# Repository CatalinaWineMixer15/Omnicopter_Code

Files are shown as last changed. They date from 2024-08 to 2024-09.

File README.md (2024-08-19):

The zip file contains all of the python code necessary to get the omnicopter up and running with the MoCap system. It contains all of the different commands 
you could run in the MoCap room. In order to interface with the MoCap room at AFIT, you will need to go to http://www.nykl.net/aburn/ and follow Dr. Scott Nykl's instructions 
in his Youtube video (https://www.youtube.com/watch?v=hPGZf2dHSG0&t=637s). You might need Dr. Nykl's permission in order to access the aftrburner code. In the youtube video, 
you will only need to follow the instructions up until the 10:30 mark or so (before you compile the code). Once you follow the instructions, you will receive the 
optitrack_viewer program which allows you to connect to the cameras in the room. You will also need to have the Motive software running on a separate computer. In Motive, the 
omnicopter should be a defined object. If it is not, then you will need to build a new object for the omnicopter (see additional resources on how to do that). The 
omnicopter will have reflective markers around it, which allows the MoCap cameras to see the omnicopter.

Additionally, to access the flight control software running on the Kakute H7, you will need to connect your computer to the Kakute via USB and run QGroundControl. QGroundControl
can be downloaded from the following website: http://qgroundcontrol.com/

If you need to access the AM32 firmware on the ESCs, you can visit the following websites: https://esc-configurator.com/ or https://am32.ca/
You can use either website to access the firmware. **NOTE** AM32 can only be accessed when you have Betaflight running on your Kakute. It will not work with QGroundControl. You
must flash between the two FC softwares in order to access AM32. To flash Betaflight on the Kakute, you must first download the Betaflight configurator: https://betaflight.com/download
Once it is downloaded, hold down the bootloader button on the Kakute while connecting the USB cable from your computer. In the Betaflight configurator, you will see that the Kakute is
now in DFU mode. Go to the firmware flasher tab, choose the correct board and firmware version, and then click on 'Load Firmware [Online]'. Finally, flash the firmware and you should
have Betaflight on the Kakute once it is done flashing. In Betaflight, make sure to select an octocopter model. Otherwise, the AM32 firmware will not know how many motors you have on
the omnicopter. To flash back to QGroundControl/PX4, go back into the Betaflight configurator Firmware Flasher tab. Click on 'Load Firmware [Local]' and select the hex file that is
included in this repo titled 'holybro_kakuteh7_bootloader.hex'. You will then be able to connect to QGroundControl. In QGroundControl, go to the Firmware tab and select a custom
px4 file that is included in this repo titled 'holybro_kakuteh7_default.px4'. Lastly, go to the Parameters tab in QGroundControl and load the saved parameters. A copy of the latest
parameters titled 'kakuteh7Param.params' is included in this repo.

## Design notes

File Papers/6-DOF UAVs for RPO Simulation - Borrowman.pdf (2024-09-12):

### 6-DOF UAVs for RPO Simulation

### Matthew N. Borrowman Air Force Institute of Technology David H. Curtis Air Force Institute of Technology

ABSTRACT

Rendezvous and proximity operations (RPO) started early on in humans’ journey to space. This has allowed for satellites and spacecraft to dock with each other, and for us to build amazing machines. Among the things possible from this concept are the International Space Station and Hubble Telescope. The manning and upkeep of both rely on RPO to be completed consistently. Additionally, RPO is becoming increasingly useful in the military and private space sectors. However, hardware testing for close proximity trajectories can often be cost prohibitive. Using a 6 degree of freedom (DOF) unmanned aerial vehicle (UAV) to simulate spacecraft missions and test payloads helps alleviate testing costs and accelerate development. These UAVs, called omnicopters, can move in any direction at any arbitrary orientation. This allows for more accurate simulation of on-orbit conditions without being in space. These machines are relatively cheap to build and operate, costing no more than commercially available UAVs. This could not only help reduce the upfront research and development costs but also help increase the number of payloads that get to orbit. We have assembled the frame and components needed for the operation of the omnicopter but have not been able to get the software to operate as intended.

### 1. INTRODUCTION

John F. Kennedy’s famous “We Chose to go to the Moon” speech helped kick off a space race that eventually put humans on the moon. To achieve this feat, NASA had a lot to learn about space operations and what was truly possible. This resulted in a handful of years long programs and many manned space launches. They tested the physiological effects of space on humans, extravehicular activity, or space walks, and, in the late stages of the Gemini program, the ability of two spacecraft to meet up and dock while orbiting our planet.[6] The demonstration of RPO had implications that reached far beyond getting to the moon.

In the 1960’s, space travel was a wildly expensive endeavor. Everything had to be built from the ground up, and lessons about how to operate in space cost both money and lives. Today, space is frequented by both countries and companies, although this is primarily with unmanned operations. In recent years, the cost of a space launch has been reduced considerably through the advent of reusable booster rockets. However, getting to space is still expensive at about $1,500/kg to low earth orbit being the cheapest.[7] The cost of launch falls on top of the development of the spacecraft and their payloads themselves. Extensive testing is needed to ensure smooth operation of these payloads when they finally reach their destination in orbit. To accomplish this, both software and hardware simulations are carried out. Software simulation has relatively low barrier to entry and is quite cost effective as the computing power needed is easily accessible. However, hardware-in-the-loop testing remains an expensive and specialized undertaking. There are various forms of hardware testing that each have their own advantages and disadvantages. Air bearing platforms are commonly used but require a dedicated workspace and cannot actuate all six degrees of freedom.[8]

Ideally, the most accurate testing of hardware would be done in space itself. This would allow for the full 6-DOF behavior necessary to test a system in its entirety. However, in most cases this is not feasible due to the cost and dangers of failure. The various forms of RPO simulation help address the different kinds of tests needed to verify the performance of these spacecraft and their payloads.[2] Kinematic simulations deal with an external actuator implementing the translational and rotational characteristics of the spacecraft flight. Dynamic simulators rely on isolating the platform and use actuators that are representative of what the actual spacecraft uses.[5] These can also be combined into hybrid systems that allow for varied aspects of the spacecraft and payload to be tested. Other platforms are available, such as specialized aircraft operating in a parabolic flight path which helps simulate the microgravity/freefall environment. These aircraft are expensive to operate and only a few examples exist.

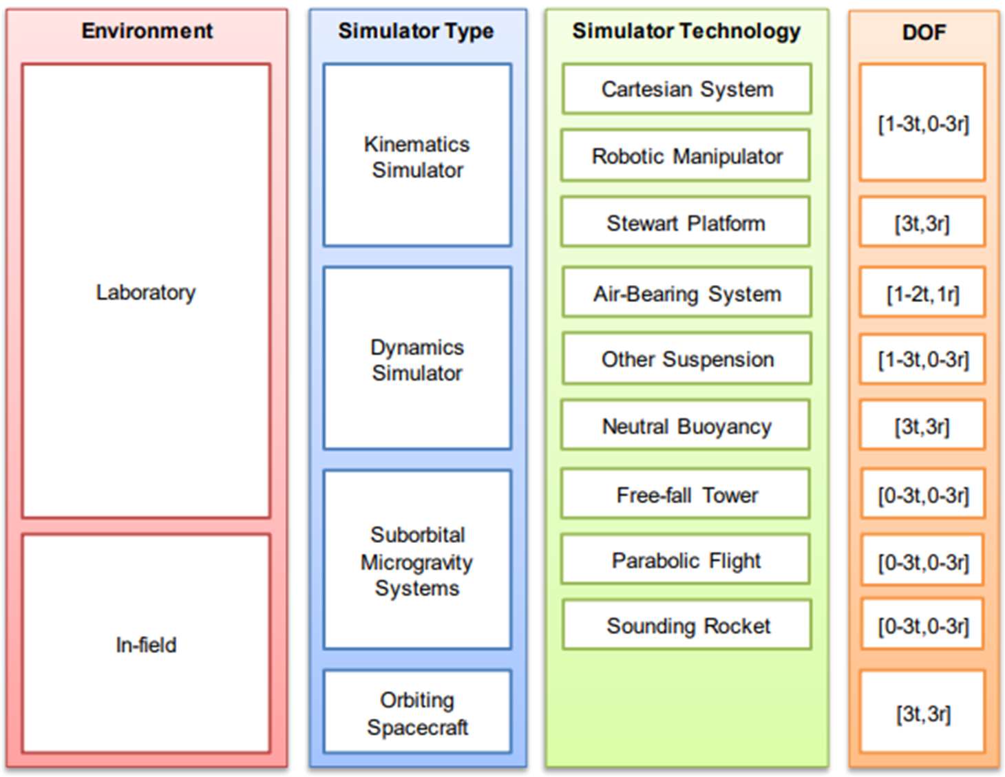
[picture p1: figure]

Figure 1. RPO Simulation Types[5]

The addition of a 6-DOF UAV, dubbed an omnicopter, could help with hardware testing. A drone that has command over the 6 degrees of freedom – 3 degrees of attitude and 3 degrees of position – is a relatively new concept with a handful of proven designs.[1][2] This opens a new avenue of hardware testing and simulation and helps address many problems that arise with the other testing methods. These drones are much more portable, cost-effective, and accessible than the dedicated testing facilities located at a handful of locations throughout the world. Additionally, multiple drones are able to be flown at the same time. This allows for multi-vehicle, 6-DOF, hardware simulations to be conducted. This has the potential to be a huge breakthrough for RPO simulation and component design. Before, almost all hardware simulations involved a singular moving vehicle.[5] Which is adequate for testing a singular payload, but testing multiple payloads designed to work in conjunction with each other is a more complicated endeavor.

### 2. METHODOLOGY

### 2.1 Design inspiration

While there are various 6-DOF UAV designs available, this project attempts to replicate the design of Brescianini and D'Andrea.[1] This design was chosen due to the availability of instruction on the build process as well as its demonstrated ability to operate with a payload. A few modifications were made for our specific design constraints, however due to the off-the-shelf nature of the build, there should not be any issue with using different parts. The open cube design and use of 8 props give it better lifting ability and modularity when compared to other designs that have been made. Examples of both can be seen in the figure below.

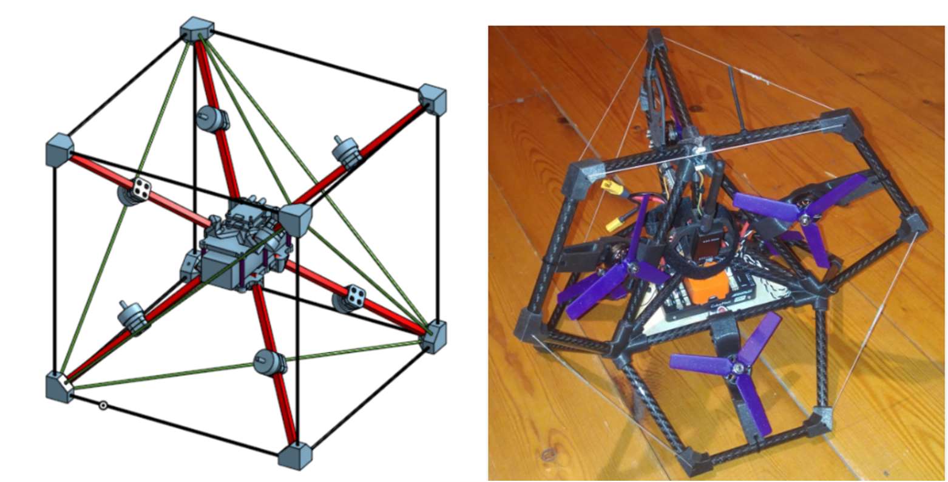
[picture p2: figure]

Figure 2. 6-DOF UAV designs[1]

The Brescianini and D'Andrea design can be seen on the left whereas the design on the right is from Peter Hall. Both utilize carbon fiber frames with 3D printed parts. However, the Brescianini and D'Andrea design is larger with the previously mentioned central area that could be payload capable. Hall’s design makes for a good 6-DOF demonstrator, but its utility outside of that scope is small. The control laws of the two designs are also significantly different due to the difference in the number of props.[1][4]

### 2.2 Starting the Build

Our build was guided by the PX4 write up that replicates the Brescianini and D’Andrea design. Included in this are complete 3D models of the system as well as STL files of all 3D printed parts. Below is the parts list.

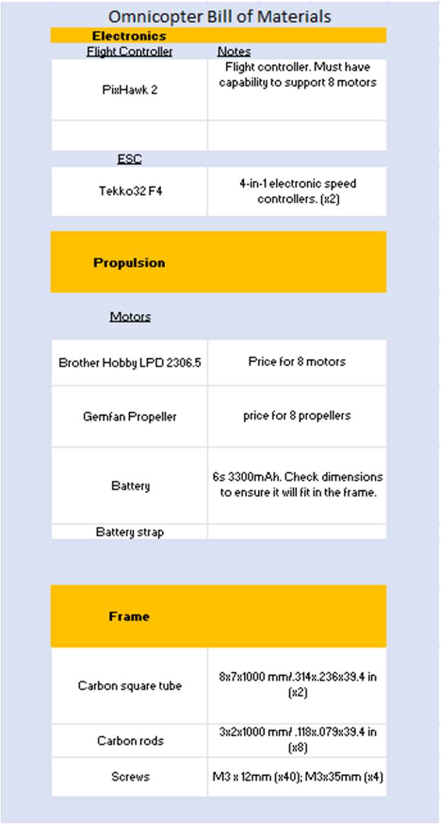
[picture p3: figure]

Figure 3. Omnicopter Parts List

The omnicopter utilizes 3D printed middle section plates, frame corners, and motor mounts. The middle section and the frame corners were printed with PLA and the motor mounts were printed with ABS. The carbon composite pieces that make up the frame were cut using a handheld rotary tool with a cutoff wheel. The eight, 8mm square tubes that the motors are mounted on are 240mm in length. The 3mm diameter rods that make up the exterior frame measure 328mm in length.

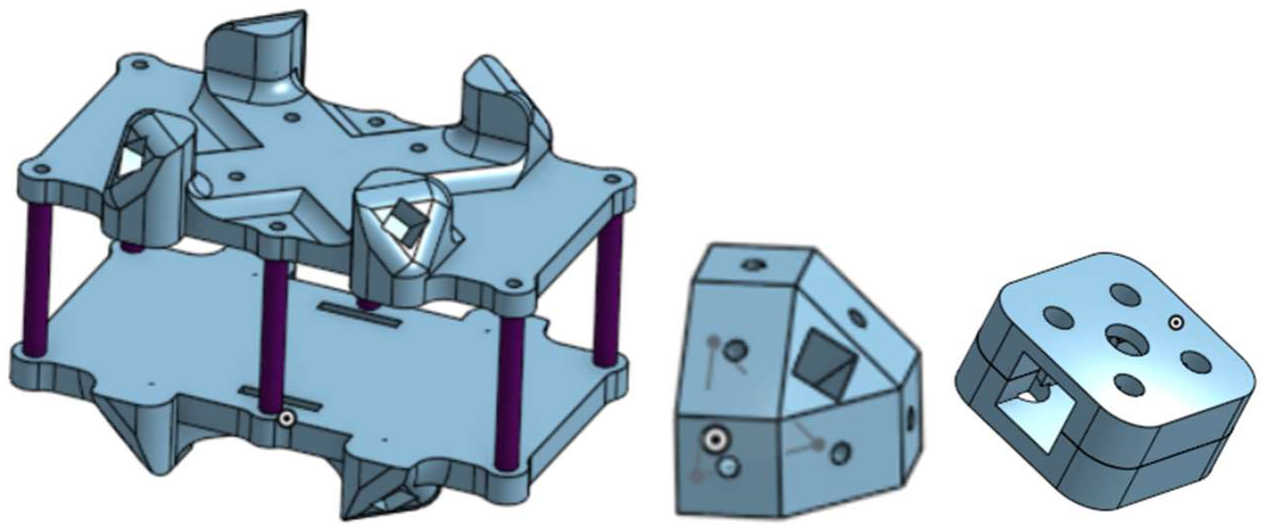
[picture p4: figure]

Figure 4. 3D Printed Assembly Parts

The motors were mounted using the 3D printed fitting shown on the right side of Figure 4. This simply clamps onto the square carbon tube with four screws. They were mounted as far away from the center as possible without the props breaking the plane of the exterior frame. It is important to mount the motors so their relative orientations are correct. Failure to do so would result in difficulty controlling the vehicle and potentially make it impossible to operate in 6 degrees of freedom.
The battery chosen was a 6s 3300mAh unit. This is mounted in the middle of the frame and held in place by the pressure from the top and bottom plates. Multiple manufacturers make this type of battery, but their dimensions can vary. It is important to verify that the battery will fit prior to purchase.
The electronic speed controllers (ESCs) were mounted on the top part of the middle section using 4 through bolts with the supplied vibration dampers. Two, 4-in-1 ESCs were used as a compact solution to power the 8 different motors. A battery connector was soldered onto the controllers, and a custom wiring harness was made to connect the ESCs to the motors.
A Pixhawk 2.1 auto pilot was used with a mini carrier board. This deviates from the original design and was used to satisfy the U.S. government purchasing requirements. The use of this part is suitable for the build, however there are lighter options available if purchasing requirements are not present. The Pixhawk was mounted on the bottom of the middle section using Velcro strips and further secured using a strip of tape. The default forward orientation of the Pixhawk was placed in such a way that the number 1 motor is in the most positive octant of the vehicle. A custom wiring harness was made to connect the ESCs to the auto pilot.

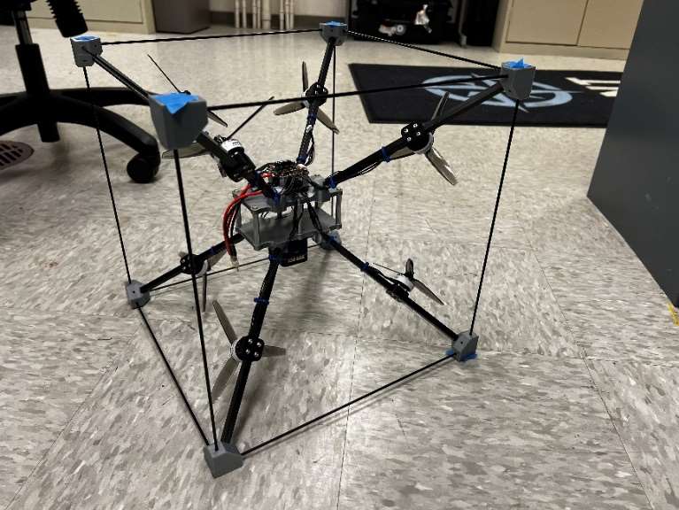
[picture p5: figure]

Figure 5. Omnicopter with ESCs and Autopilot Mounted

After mounting the auto pilot, a telemetry link was added. While there are many options for telemetry links, we tried to use the lightest solution we had on hand. The telemetry range and power requirements for this application are negligible. This telemetry link allows for the ground station to connect wirelessly to the auto pilot. This can be used to set up parameters for the operation of the omnicopter, as well as set up missions and flight paths.
These are the basic components needed for operation. Our design chose to use a Vicon chamber to give the autopilot positioning data in lieu of actual GPS connectivity. This decreases the weight of our design but also limits it to indoor operation. If outdoor operation is desired, a GPS antenna would be needed for the autopilot to get positioning data.
Programming the correct settings for the omnicopter is a difficult endeavor as there is not default omnicopter setting. Our build opted to use the QGroundControl ground station and run the PX4 firmware on the autopilot. For the airframe setup, a generic multi-rotor airframe much be chosen, and the motor positions need to be set up in a three-dimensional space instead of a coplanar setup found in most traditional multi-rotor aircraft.

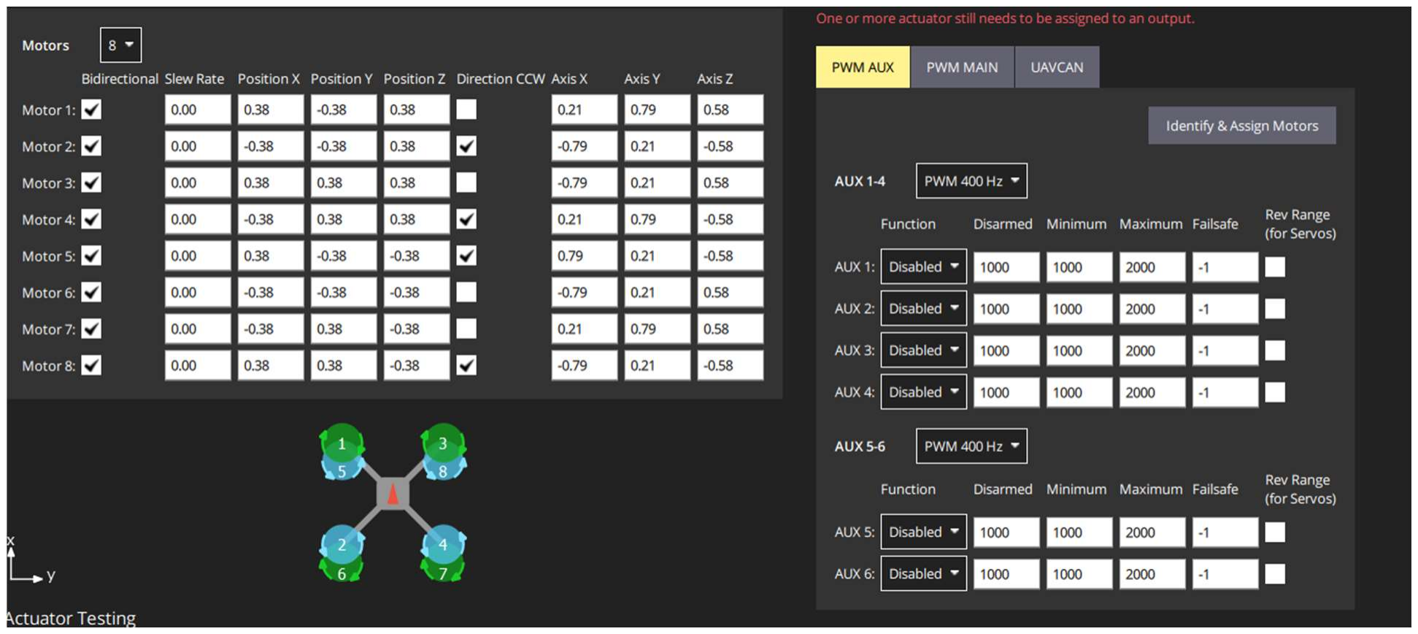
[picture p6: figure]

Figure 6. Omnicopter airframe setup

Using the indicated positive axis on the software, the known positive position of the autopilot, and the motor numbering scheme from the ESC data sheet, the location and orientations of the motors was able to be programmed. The positions are measured in feet from the center of the omnicopter. The orientation axes are normalized and based on where the motor shafts are pointing in relation to the positive axis of the omnicopter.

### 3. RESULTS

The omnicopter hardware has been assembled, however, it has not gotten off the ground yet. Our suspicion is that a failsafe is being triggered in the software that is preventing the system from operating. Our current troubleshooting hasn’t provided additional insight onto what the exact solution to this problem is.

### 4. CONCLUSIONS AND FUTURE WORK

The omnicopter is an ongoing design challenge. We hope to achieve the maiden flight soon and demonstrate the ability to manipulate the 6 degrees of freedom made possible with this design. After the flight characteristics have been figured out, we hope to add a payload. This could be an actuator or a sensor that could be used for testing. We also hope to make more examples and run multiple vehicle missions to simulate an on-orbit RPO.

### 5. REFERENCES

[1] Brescianini, D., and D’Andrea, R., Design, Modeling and Control of an Omni-Directional Aerial Vehicle. [2] | Christensen, Gargioni, Doyle, Schroeder and Black. "Space Simulation Overview: Leading Developments
| towards using Multi-Rotors to Simulate Space Vehicle Dynamics," AIAA 2020-1134. AIAA Scitech 2020 Forum. January 2020.
[3] Deans, C., Furgiuele, T., Doyle, D., and Black, J., Simulating omni-directional aerial vehicle operations for
| modeling satellite dynamics ASCEND 2020, 2020.
[4] E. Kaufman, K. Caldwell, D. Lee and T. Lee, Design and development of a free-floating hexrotor UAV for 6-
| DOF maneuvers, 2014 IEEE Aerospace Conference, Big Sky, MT, USA, 2014, pp. 1-10, doi: 10.1109/AERO.2014.6836427.
[5] Kwok Choon, Stephen & Wilde, Markus & Safbom, Conor & Romano, Marcello. (2020). Kinematic and
| Dynamic Spacecraft Maneuver Simulators for Verification and Validation of Space Robotic Systems. 10.2514/6.2020-1919.
[6] May. “What Was the Gemini Program” NASA Knows! August 2017
[7] Roberts, T., “Space Launch to Low Earth Orbit: How Much Does it Cost?” CSIS Aerospace Security Project,
| September 2022
[8] Rughani, R., Villafana, L., and Barnhart, D. A., “Swarm RPO and Docking Simulation on a 3DOF Air Bearing
| Platform,” International Astronautical Congress (IAC), 2019.

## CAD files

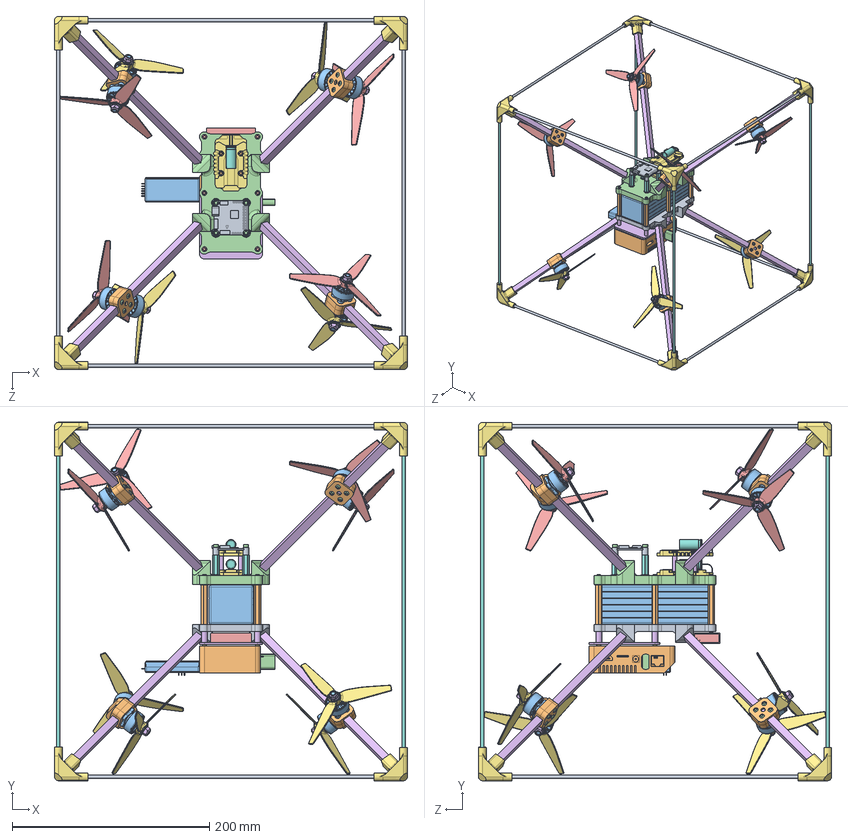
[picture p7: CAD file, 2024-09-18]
CAD/OmniFullWithMotors.SLDASM
358.1 x 363.7 x 358.2 mm
BottomBodyPlate_Simple
BodyPlate_Column x 6
BodyColumn_Washer x 10
ModifiedPart_Simple
BodyPlate_Bolt x 8
ODROID_Platform
BodyPlate_BottomBolt x 4
FC_Column x 4
FC_Board
ODROID
ODROID_SerialAdapter
ODROID_WifiModule
ODROID_SD_Card
ESC_Columns x 4
SkyStarsESC x 2
ESC_Capacitor x 2
ESC_BottomBolt x 4
ESC_TopBolt x 4
Battery
FC_Bolt2 x 8
JETI_Antenna
Rod x 8
CornerPart_v3_FlatCorner_2mmWall_3p5mmRod_p4mmTol x 8
Tube_Vert x 4
Tube_Horiz x 8
MotorMountPiece x 16
Motor x 8
Motor_Bolt x 32
PropCW x 4
MotorNut x 8
PropCCW x 4

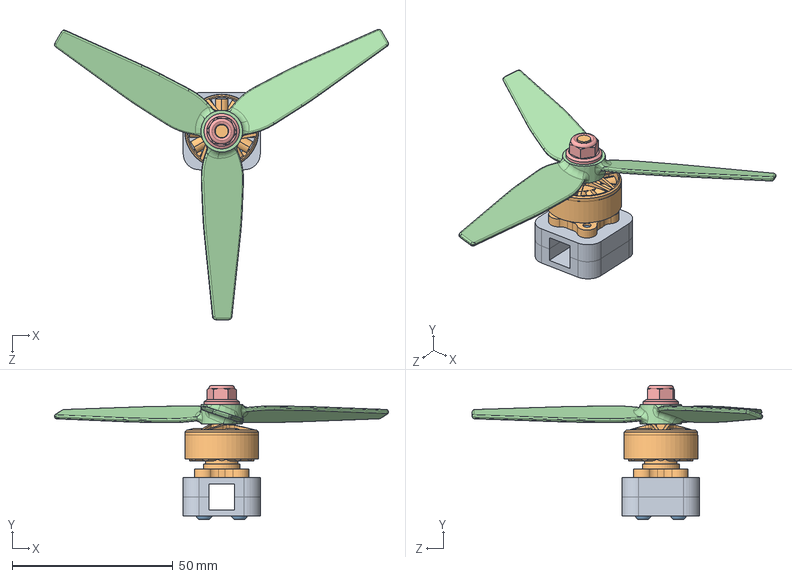
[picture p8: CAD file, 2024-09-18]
CAD/MotorAssemblyCW.SLDASM
103.9 x 41.9 x 90.4 mm
MotorMountPiece x 2
Motor
Motor_Bolt x 4
PropCW
MotorNut

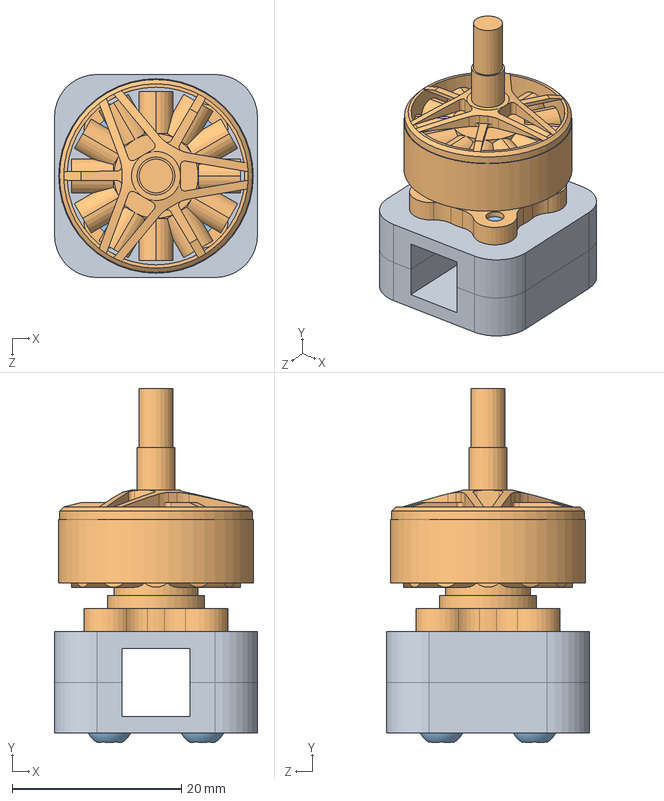
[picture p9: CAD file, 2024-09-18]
CAD/MotorAssembly.SLDASM
24.0 x 41.9 x 24.0 mm
MotorMountPiece x 2
Motor
Motor_Bolt x 4

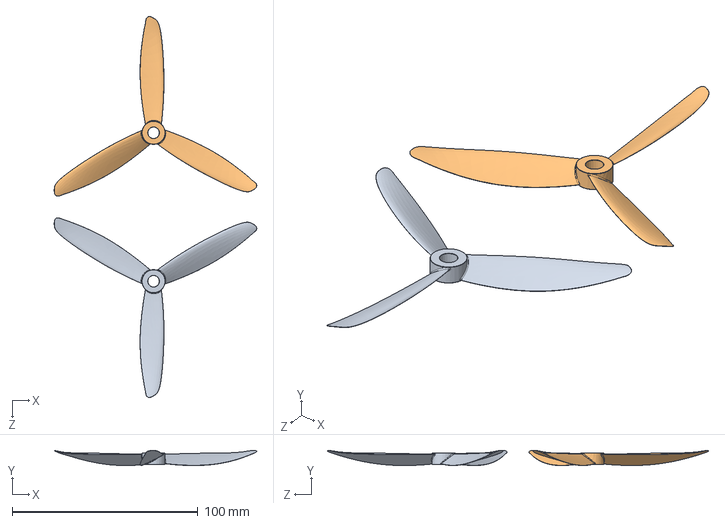
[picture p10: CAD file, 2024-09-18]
CAD/Tri-Blade 5045 Propeller CCW.SLDASM
109.2 x 8.15 x 205.3 mm
5045 CCW.step
5045 CW.step

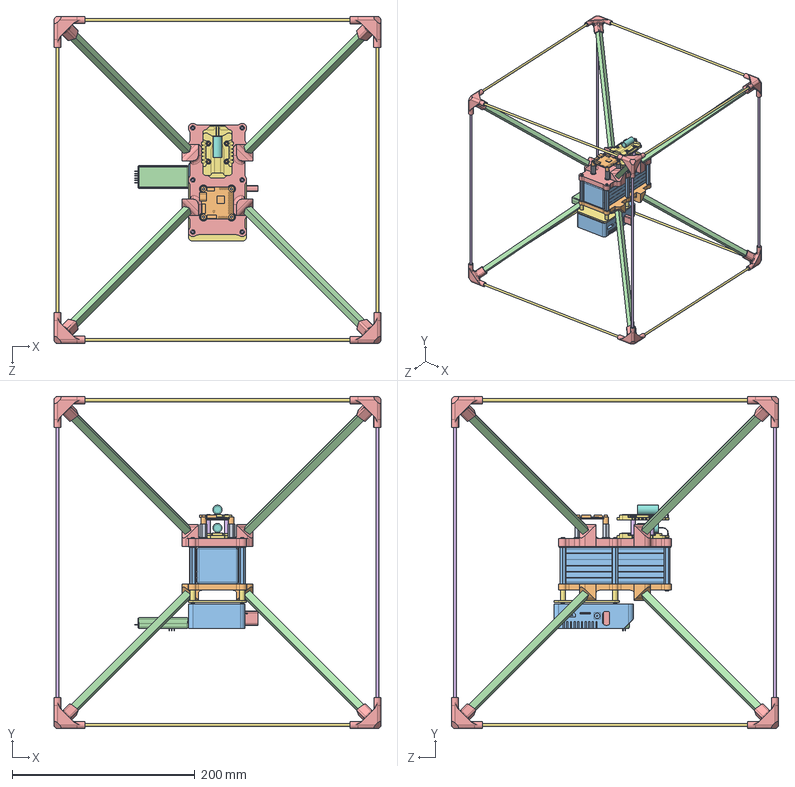
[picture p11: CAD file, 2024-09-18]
CAD/OmniFull.SLDASM
358.1 x 363.7 x 358.2 mm
BottomBodyPlate_Simple
BodyPlate_Column x 6
BodyColumn_Washer x 10
ModifiedPart_Simple
BodyPlate_Bolt x 8
ODROID_Platform
BodyPlate_BottomBolt x 4
FC_Column x 4
FC_Board
ODROID
ODROID_SerialAdapter
ODROID_WifiModule
ODROID_SD_Card
ESC_Columns x 4
SkyStarsESC x 2
ESC_Capacitor x 2
ESC_BottomBolt x 4
ESC_TopBolt x 4
Battery
Rod x 8
CornerPart_v3_FlatCorner_2mmWall_3p5mmRod_p4mmTol x 8
Tube_Vert x 4
Tube_Horiz x 8

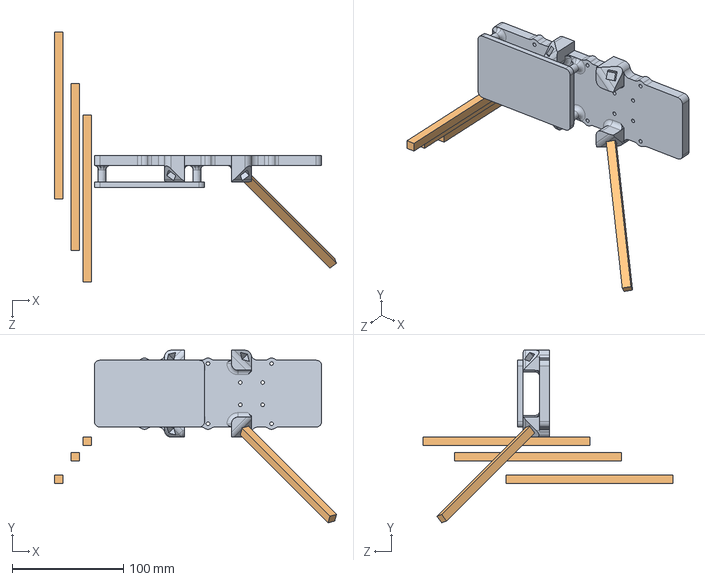
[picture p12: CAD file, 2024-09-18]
CAD/Omni.SLDASM
253.0 x 154.9 x 224.2 mm
ModifiedPart
Rod x 4

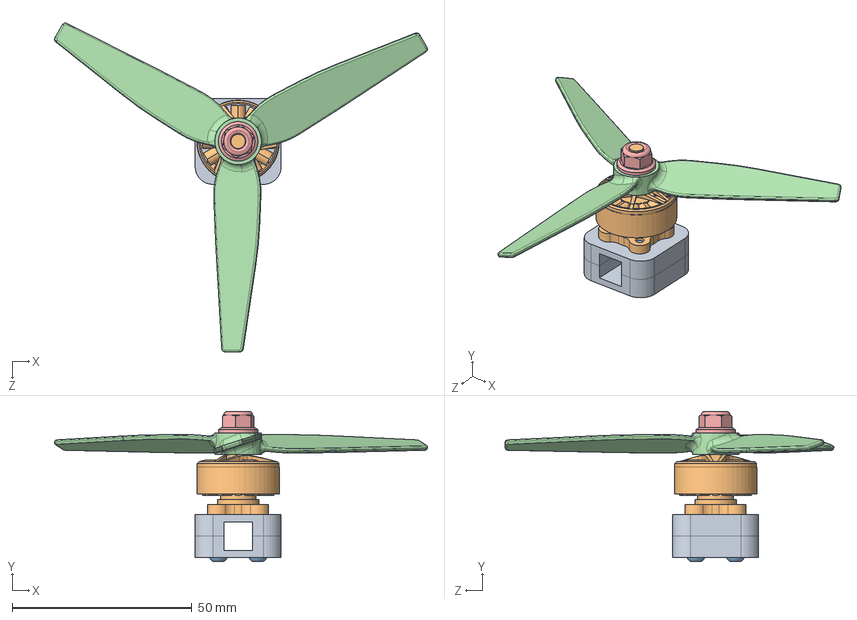
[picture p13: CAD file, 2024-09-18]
CAD/MotorAssemblyCCW.SLDASM
103.9 x 41.9 x 91.6 mm
MotorMountPiece x 2
Motor
Motor_Bolt x 4
PropCCW
MotorNut

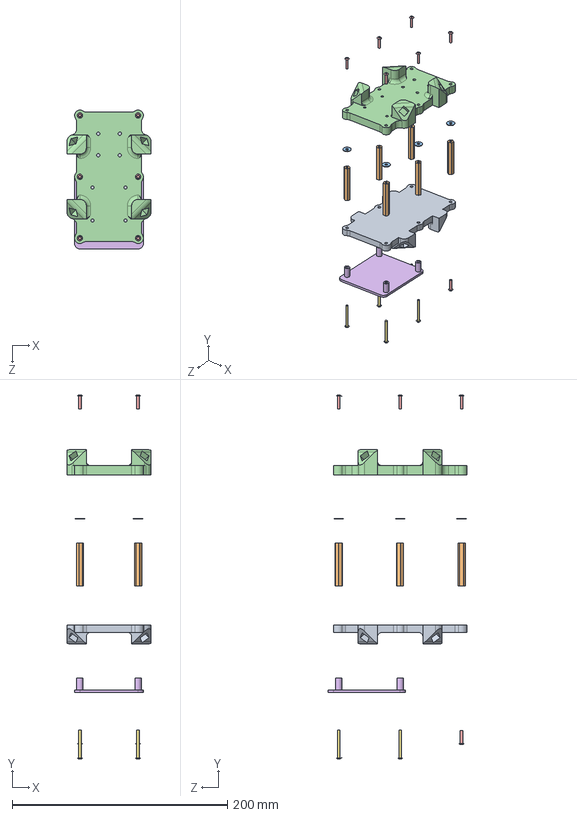
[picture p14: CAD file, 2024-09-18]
CAD/Omni_Body.SLDASM
78.0 x 338.0 x 129.0 mm
BottomBodyPlate_Simple
BodyPlate_Column x 6
BodyColumn_Washer x 6
ModifiedPart_Simple
BodyPlate_Bolt x 8
ODROID_Platform
BodyPlate_BottomBolt x 4

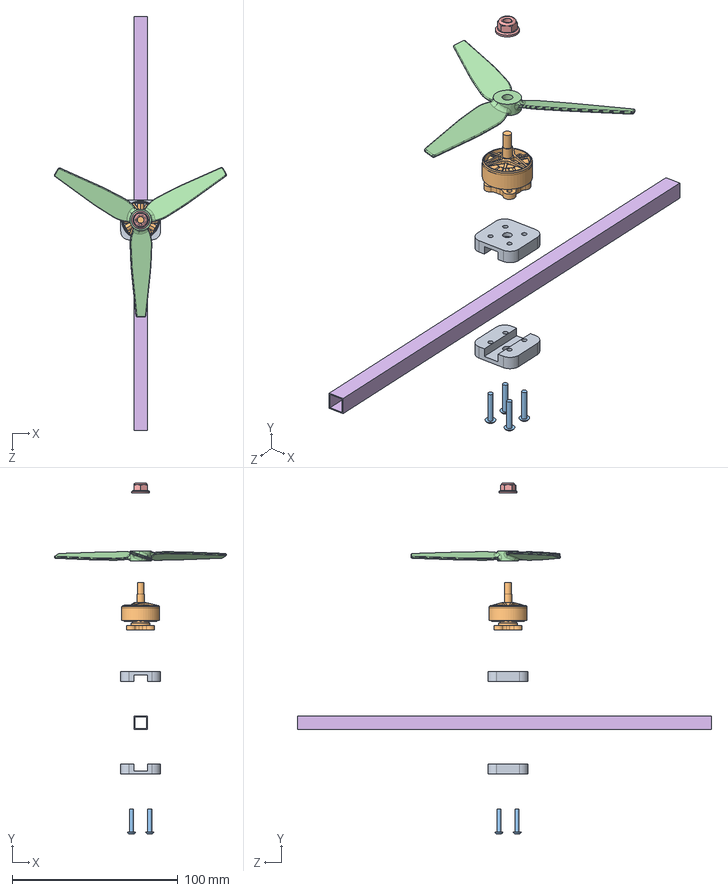
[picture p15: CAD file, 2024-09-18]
CAD/MotorAssemblyWithRod.SLDASM
103.9 x 211.9 x 250.0 mm
MotorMountPiece x 2
Motor
Motor_Bolt x 4
PropCW
MotorNut
Rod

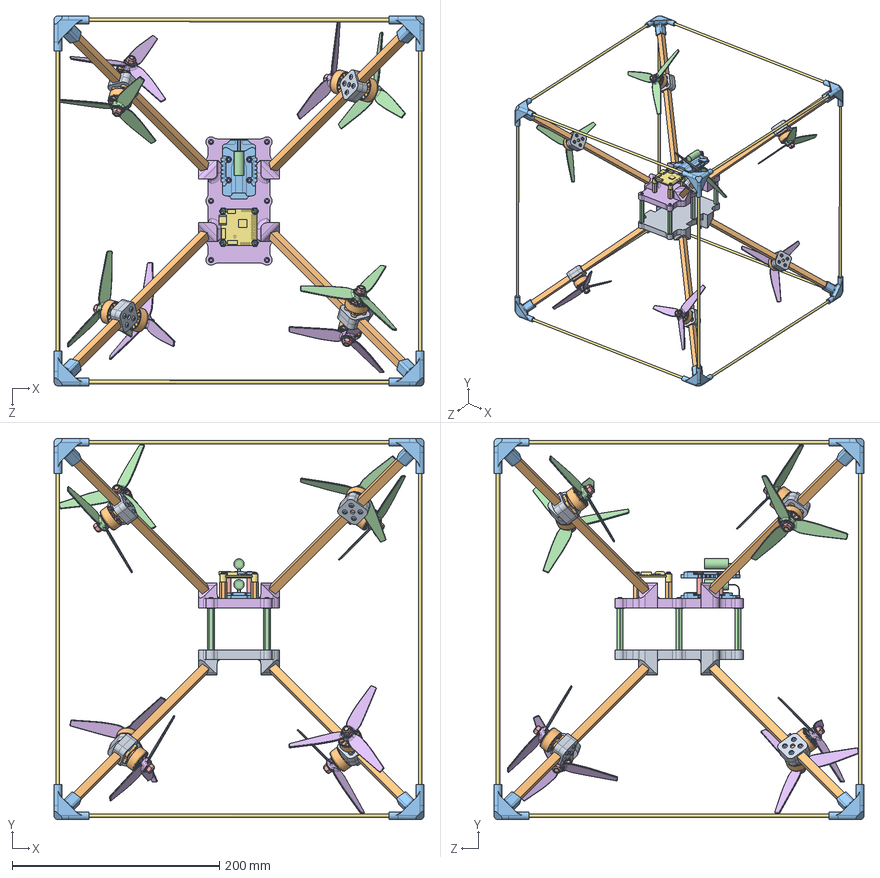
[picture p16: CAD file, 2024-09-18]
CAD/Omni_NEW.SLDASM
357.0 x 367.9 x 357.1 mm
BottomBodyPlate_Simple
Rod x 8
CornerPart_v3_FlatCorner_2mmWall_3p5mmRod x 8
BodyPlate_Column x 6
BodyColumn_Washer x 6
ModifiedPart_Simple
Tube x 12
ESC_BottomBolt x 4
BodyPlate_Bolt x 6
FC_Column x 4
SkyStarsESC x 2
ESC_Capacitor x 2
ESC_Columns x 4
ESC_TopBolt x 4
FC_Board
FC_Bolt x 4
MotorMountPiece x 16
Motor x 8
Motor_Bolt x 32
PropCW x 4
MotorNut x 8
PropCCW x 4

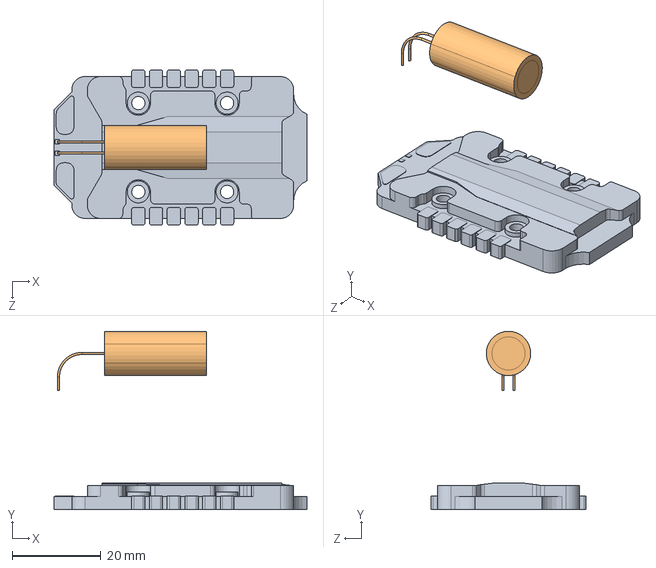
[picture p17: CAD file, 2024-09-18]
CAD/SkyStarsESCAssembly.SLDASM
57.0 x 40.2 x 35.0 mm
SkyStarsESC
ESC_Capacitor

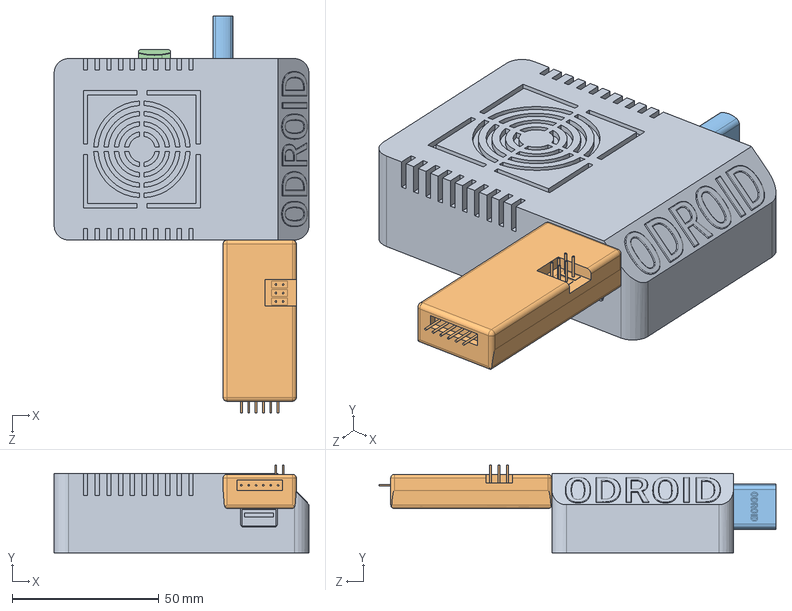
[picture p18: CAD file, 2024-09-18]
CAD/ODROID_Assembly.SLDASM
87.0 x 29.9 x 135.5 mm
ODROID
ODROID_SerialAdapter
ODROID_WifiModule
ODROID_SD_Card

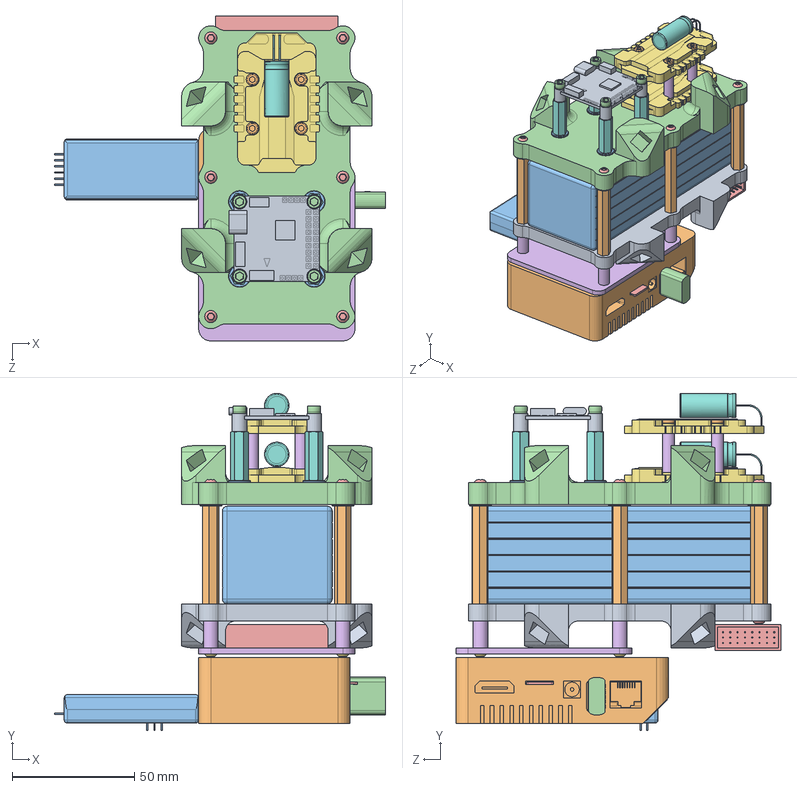
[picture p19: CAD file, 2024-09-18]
CAD/Omni_BodyWithBoards.SLDASM
135.5 x 138.1 x 133.0 mm
BottomBodyPlate_Simple
BodyPlate_Column x 6
BodyColumn_Washer x 10
ModifiedPart_Simple
BodyPlate_Bolt x 8
ODROID_Platform
BodyPlate_BottomBolt x 4
FC_Column x 4
FC_Board
ODROID
ODROID_SerialAdapter
ODROID_WifiModule
ODROID_SD_Card
ESC_Columns x 4
SkyStarsESC x 2
ESC_Capacitor x 2
ESC_BottomBolt x 4
ESC_TopBolt x 4
Battery
FC_Bolt2 x 8
JETI_Antenna

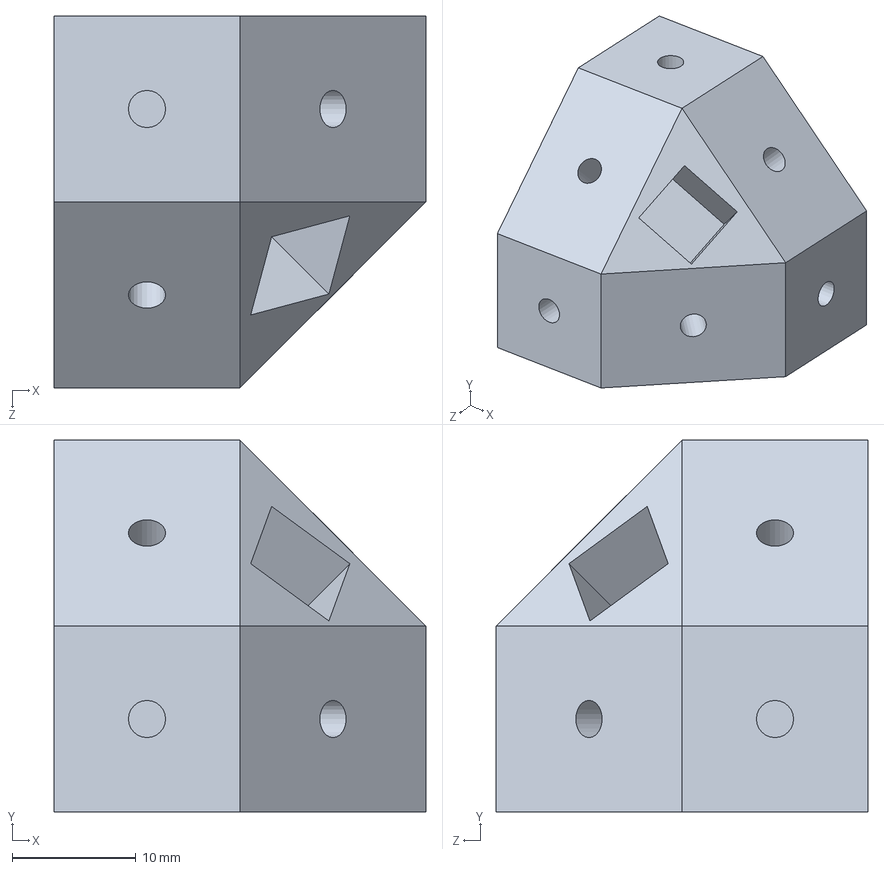
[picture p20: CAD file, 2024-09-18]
CAD/CornerPart.SLDPRT
30.0 x 30.0 x 30.0 mm

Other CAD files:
CAD/Tri-Blade 5045 Propeller.SLDASM
CAD/CornerPart_v3_2mmWall.SLDPRT
CAD/ODROID_SD_Card.SLDPRT
CAD/BottomBodyPlate_Simple.SLDPRT
CAD/3DPrintedCornerOutside.stl
CAD/Battery.SLDPRT
CAD/BodyColumn_Washer.SLDPRT
CAD/BodyPlate_Bolt.SLDPRT
CAD/BodyPlate_BottomBolt.SLDPRT
CAD/BodyPlate_Column.SLDPRT
CAD/CornerPart_v2.SLDPRT
CAD/CornerPart_v3.SLDPRT
CAD/CornerPart_v3.STL
CAD/CornerPart_v3_2mmWall.STL
CAD/CornerPart_v3_2mmWall_3mmSquare.SLDPRT
CAD/CornerPart_v3_2mmWall_3p5mmRod.SLDPRT
CAD/CornerPart_v3_2mmWall_3p5mmRod.STL
CAD/CornerPart_v3_FlatCorner_2mmWall_3p5mmRod.SLDPRT
CAD/CornerPart_v3_FlatCorner_2mmWall_3p5mmRod.STL
CAD/CornerPart_v3_FlatCorner_2mmWall_3p5mmRod_p2mmTol.SLDPRT
CAD/CornerPart_v3_FlatCorner_2mmWall_3p5mmRod_p2mmTol.STL
CAD/CornerPart_v3_FlatCorner_2mmWall_3p5mmRod_p4mmTol.SLDPRT
CAD/CornerPart_v3_FlatCorner_2mmWall_3p5mmRod_p4mmTol.STL
CAD/ESC_BottomBolt.SLDPRT
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

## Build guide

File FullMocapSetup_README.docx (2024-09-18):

# Omnicopter Project

# Full Motion-Capture Setup

September 2024

# Optitrack/Motive

## Hardware requirements

1. OptiTrack camera and computer system.
2. Retroreflective markers and adhesive
  a. Used Command strips cut into squares

## Initial setup

1. Start Motive application.
2. Follow the instructions here (https://docs.optitrack.com/motive/rigid-body-tracking) to attach the markers to the omnicopter body and create a rigid body object in Motive.
  a. Note: name the object something recognizable such as “omnicopter”.

## Each run

1. Start Motive application.

# Ground Control Station (GCS) Computer

## Machine requirements

1. Windows 10 (TODO: and 11?)
2. Ethernet port to connect to the Optitrack system
3. Ability to broadcast a Wifi hotspot from the computer

## QGroundControl

### Initial setup

1. Follow the instructions in this link to install QGroundControl onto the GCS: https://docs.qgroundcontrol.com/master/en/qgc-user-guide/getting_started/download_and_install.html

### Each run

1. Open QGroundControl and wait for the status in the top left corner to change from “Disconnected” to another status (usually “Ready” or “Not Ready”).

## Motive Connection

### Initial setup

1. Set up the ethernet connection:
  a. Connect via ethernet cable to lab computer running Motive and connected to Optitrack camera array.
  b. Open ControlPanel -> Network and Internet -> Network and Sharing Center and click “Change adapter settings” on the left side of the window.
  c. Right-click on the ethernet device being used by the Motive ethernet connection and select “Properties”.
  d. Under the Networking” tab, double-click on “Internet Protocol Version 4 (TCP/IPv4)”.
  e. Select “Use the following IP address” and enter these values for the following fields:
- IP address: 192.168.11.3
- Subnet mask: 255.255.255.0
  f. TODO: Also mention DNS server addresses?
  g. Click “OK”, then “OK”.
  h. Close the network windows.
2. Install AftrBurner/OptiTrack_Viewer
  a. Follow the instructions in this YouTube video (https://youtu.be/hPGZf2dHSG0) from timestamps 0:00 to 10:32 to install AftrBurner onto the computer.
  b. Extract the “optitrack_viewer-omnicopter.zip” file located in the “GCS” repo directory and copy the whole folder to the directory “C:\repos\aburn\usr\hub”.

### Each run

1. Connect to OptiTrack ethernet:
  a. Connect via ethernet cable to lab computer running Motive and connected to OptiTrack camera array.
2. Begin reading OptiTrack data onto the GCS:
  a. Run the “OptiTrack_Viewer.exe” executable located in the directory “C:\repos\aburn\usr\hub\optitrack_viewer-omnicopter\cwin64”.
  b. A window should appear titled “AftrBurner Engine”.
  c. In that window, click “Mocap Tools” in the “Menu” window, then “Show Object Viewer”.
  d. In the “Object Viewer” window, click “CONNECT”.
  e. Ensure that the “omnicopter” object is checked under the list of available models.
  f. Select “omnicopter” relative to “origin”.

## Ubuntu/WSL

### Installation

We used Windows WSL 1 and Ubuntu 20.04:

1. Install WSL 1/Ubuntu 20.04 from Microsoft Store: https://apps.microsoft.com/detail/9mttcl66cpxj?hl=en-us&gl=US

### Additional Packages

#### Python 3

Used to send commands and/or receive data in the network.

Install using the following command in the Ubuntu terminal:

- sudo apt install python3

#### MAVSDK

High-level Python functions used to create MAVlink messages.

Install following the instructions in the Quick Start Guide.

Quick Start: https://mavsdk.mavlink.io/main/en/python/quickstart.html

API Docs: http://mavsdk-python-docs.s3-website.eu-central-1.amazonaws.com/

#### Asyncio

Python library used for asynchronous function calls; included natively in standard Python 3.

Reference: https://docs.python.org/3/library/asyncio.html

#### PyMap3d

Python library for 3D geographic coordinate conversions.

Install using the following command:

- pip install pymap3d

Reference: https://pypi.org/project/pymap3d/

## ODROID Connection

### Initial setup

1. Set up Mobile Hotspot:
  a. Either search “Mobile Hotspot” in the Windows search bar or navigate to Settings -> Network and Internet -> Mobile Hotspot.
  b. Edit the username and password to match what will be used on the ODROID.

### Each run

1. Turn on hotspot:
  a. Either search “Mobile Hotspot” in the Windows search bar or navigate to Settings -> Network and Internet -> Mobile Hotspot.
  b. Toggle the switch to “ON”.
2. Power on ODROID and wait for it to connect to the hotspot.
3. Send mocap data to ODROID:
  a. Open Ubuntu to the “scripts” repo directory containing “forwardmocap.py”.
  b. Run the command:
- python3 forwardmocap.py
  c. Once the connection is established between Motive, the ground station computer, and the ODROID, the script will begin printing position and attitude updates to the Ubuntu console, indicating that the data is being sent to the ODROID.

# ODROID

## Hardware requirements

1. Monitor with HDMI cable
2. USB keyboard and mouse
3. USB Wi-Fi module (ODROID brand or otherwise)
4. FTDI USB to TTL Serial Adapter

## Login Info

- Admin username: odroid
- Password: odroid

## Serial adapter

References

1. https://docs.px4.io/main/en/companion_computer/pixhawk_companion.html#serial-port-setup
2. Amazon link for the adapter we purchased: https://a.co/d/iM7mWNy

### Initial setup

The FTDI serial adapter is used to establish a connection between the ODROID and the flight controller.

1. Follow the instructions in the PX4 docs above to map the wiring between the flight controller’s TELEM2 port and the serial adapter.
2. Plug the adapter into one of the ODROID’s USB ports.
3. Run the command “dmesg” in the ODROID terminal.
4. In the resulting output, look for the phrase “FTDI Serial Device converter now attached to...” and take note of the file path that follows (ours was “ttyUSB0”, so the resulting path is “/dev/ttyUSB0”).
5. Check to make sure the device is listed in the “/dev/” directory with the adapter connected.
6. The flight controller should already be configured to use MAVlink messages over TELEM2, but if not, make that change following the instructions in the PX4 docs above.

## Internet Connection

### Set to connect to GCS Wi-Fi hotspot automatically

1. Click the Wi-Fi symbol in the top right corner of the ODROID desktop.
2. Click “Edit Connections”.
3. Double-click on the hotspot network under the list of available Wi-Fi networks.
4. Under “General”, check the box for “Connect automatically with priority” and use the plus sign to set the priority to 1 or greater (gives preference to connecting to the hotspot over other known networks).
5. Under “Wi-Fi”, select the appropriate option for “Band” for the device (the ODROID module uses 5 GHz) and the device under the options for “Device” (ours was wlan0).
6. Under “Wi-Fi Security”, set the “Security” to “WPA & WPA2 Personal” and the “Password” to the hotspot’s password if not already set.

### Potential issues

#### Missing GUI for Wi-Fi connections

Source: https://www.cyberciti.biz/faq/change-netplan-renderer-from-networkd-to-networkmanager/

If netplan (the backend program that manages network connections) is not configured to use NetworkManager, the GUI for Wi-Fi connections will not be useful for viewing available networks and connecting automatically.

To fix this problem, NetworkManager needs to be set as the “renderer” for netplan in the config file “/etc/netplan/01-netcfg.yaml” following these steps:

1. Open the ODROID terminal.
2. Backup the current config file by copying the file to another location.
3. Open the config file for editing by right-clicking on the file or entering the following command with your editor of choice:
- sudo editor /etc/netplan/01-netcfg.yaml
4. Set the renderer to NetworkManager by editing the file to appear as follows (a copy is saved in the “ODROID” directory in this repo for reference):
- network:
- version: 2
- renderer: NetworkManager
5. Apply the change by rebooting the system or entering the command:
- sudo netplan apply

#### ODROID Wi-Fi 5BK Module Driver Bug

Source: https://wiki.odroid.com/odroid-h2/application_note/howto_wifi_driver_rtl8812au

If experiencing issues connecting to Wi-Fi using this USB module, try following these instructions in the ODROID terminal to install the correct driver:

1. Install DKMS:
- sudo apt install build-essential dkms git
2. Clone the driver source from GitHub:
  - git clone https://github.com/brektrou/rtl8821CU
  - cd rtl8821CU
3. Add the driver to DKMS:
- sudo ./dkms-install.sh
4. Enable Wi-Fi in every boot:
  a. Open usb_modeswitch rules using your editor of choice:
- sudo editor /lib/udev/rules.d/40-usb_modeswitch.rules
  b. Append the following before the end line LABEL="modeswitch_rules_end":
    - # Realtek 8821CU Wifi AC USB
    - ATTR{idVendor}=="0bda", ATTR{idProduct}=="1a2b", RUN+="/usr/sbin/usb_modeswitch '/%k'"
  c. Reboot the machine or reload udev rules to apply changes without rebooting:
- sudo udevadm control –reload-rules && sudo udevadm trigger
  d. NOTE: If you lost the Wi-Fi module 5B after rebooting your system, you can re-enable that by using the following command. To do this automatically, there're so many ways to do that such as using systemd, an init script, or a Python script:
- sudo udevadm control trigger

## MAVlink-Router

References

Source: https://github.com/mavlink-router/mavlink-router

Other references:

1. https://ardupilot.org/dev/docs/raspberry-pi-via-mavlink.html

### Multiple MAVlink pathway setup

The Python script “mavserver.py” in the “scripts” directory establishes 3 “paths” between the GCS and the flight controller using specific port numbers:

1. Port 14550: Used by QGroundControl to connect to the flight controller.
2. Port 14560: Used by the “forwardmocap.py” script to send constant motion capture data to the flight controller.
3. Port 14570: Used by the user to send MAVlink commands via Python scripts.

The script can be run on the ODROID by copying it to the ODROID’s desktop and running the following command in the terminal:

- /usr/bin/python3 /home/odroid/Desktop/mavserver.py

### Initial setup

1. Install mavlink-router:

Run each of these commands in the ODROID’s terminal:

1. cd
2. git clone https://github.com/mavlink-router/mavlink-router.git ./mavlink-router
3. cd mavlink-router
4. git submodule update --init --recursive
5. sudo apt install git ninja-build pkg-config gcc g++ systemd
6. sudo pip3 install meson
7. /usr/local/bin/meson setup build .
8. ninja -C build
9. sudo ninja -C build install
2. Connect to the hotspot if not already connected.
3. Copy/recreate the “mavserver.py” script to the ODROID desktop.
4. Edit the mavserver file so that the string variable GCS_IP equals the GCS hotspot IP address and the string variable FC_path equals the path of the FTDI serial adapter.
5. Set mavserver as executable using the command:
- chmod a+rx ~/Desktop/mavserver.py
6. Set mavserver to run at device startup:

The ODROID was configured to automatically run mavserver at startup by following these steps:

1. Copy/recreate the “StartUpD.service” file located in the “ODROID” directory in the repo to the “/etc/systemd/system” directory on the ODROID.
2. Run the following command in the terminal to enable the service file:
- systemctl enable StartUpD.service

NOTE: The .service file waits for an internet connection before running, so ensure that the mobile hotspot is turned on when trying to run the script at startup.

Reference: https://unix.stackexchange.com/questions/47695/how-to-write-startup-script-for-systemd

### Future work

1. A config file should be created following the instructions on the mavlink-router GitHub, using the default location “/etc/mavlink-router/main.conf” or otherwise, and set to keep logs of all MAVlink messages for post-run analysis.

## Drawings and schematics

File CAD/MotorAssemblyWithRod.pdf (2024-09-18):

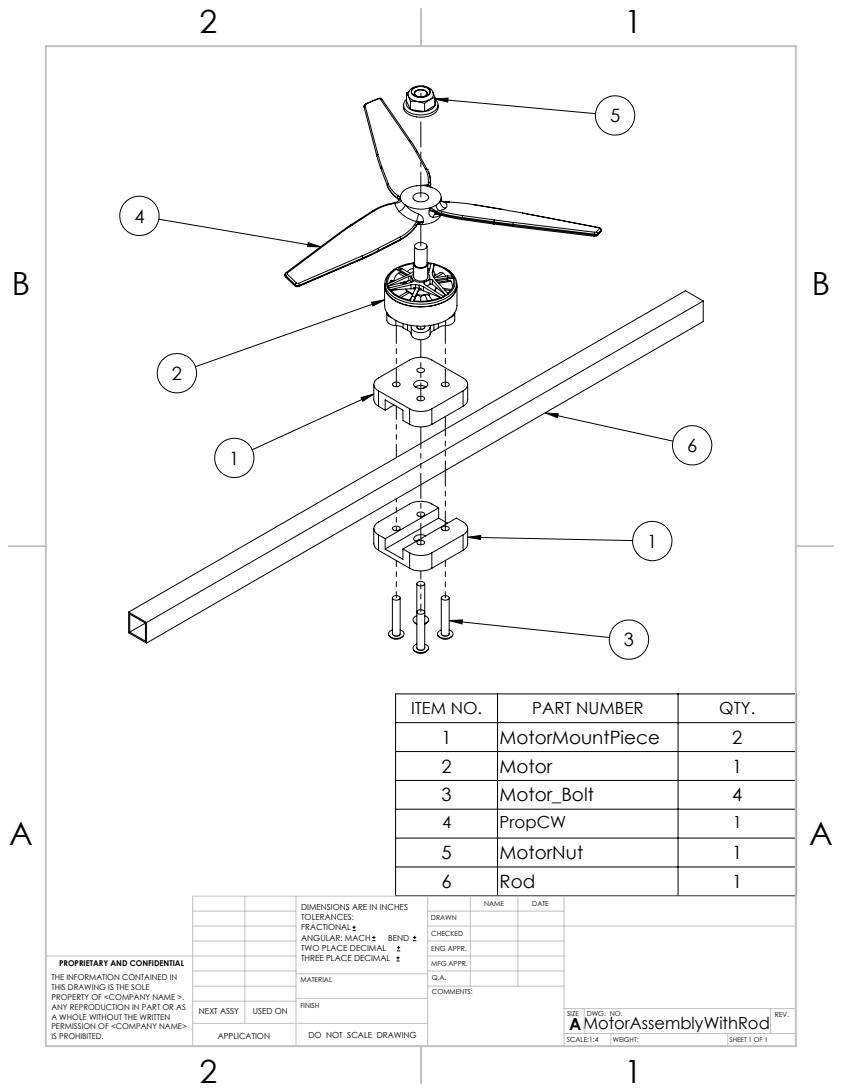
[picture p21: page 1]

ITEM NO. | PART NUMBER | QTY.
1 | MotorMountPiece | 2
2 | Motor | 1
3 | Motor_Bolt | 4
4 | PropCW | 1
5 | MotorNut | 1
6 | Rod | 1

TOLERANCES: FRACTIONAL ANGULAR: MACH BEND TWO PLACE DECIMAL THREE PLACE DECIMAL | | NAME | DATE DIMENSIONS ARE IN INCHES

DRAWN
CHECKED
ENG APPR.

PROPRIETARY AND CONFIDENTIAL THE INFORMATION CONTAINED IN THIS DRAWING IS THE SOLE PROPERTY OF <COMPANY NAME >. ANY REPRODUCTION IN PART OR AS A WHOLE WITHOUT THE WRITTEN PERMISSION OF <COMPANY NAME> IS PROHIBITED. | | | | MFG APPR.

MATERIAL | Q.A.

NEXT ASSY | USED ON | FINISH

SIZE A | DWG. NO. MotorAssemblyWithRod | REV.

APPLICATION | | DO NOT SCALE DRAWING

SCALE:1:4 | WEIGHT: | SHEET 1 OF 1

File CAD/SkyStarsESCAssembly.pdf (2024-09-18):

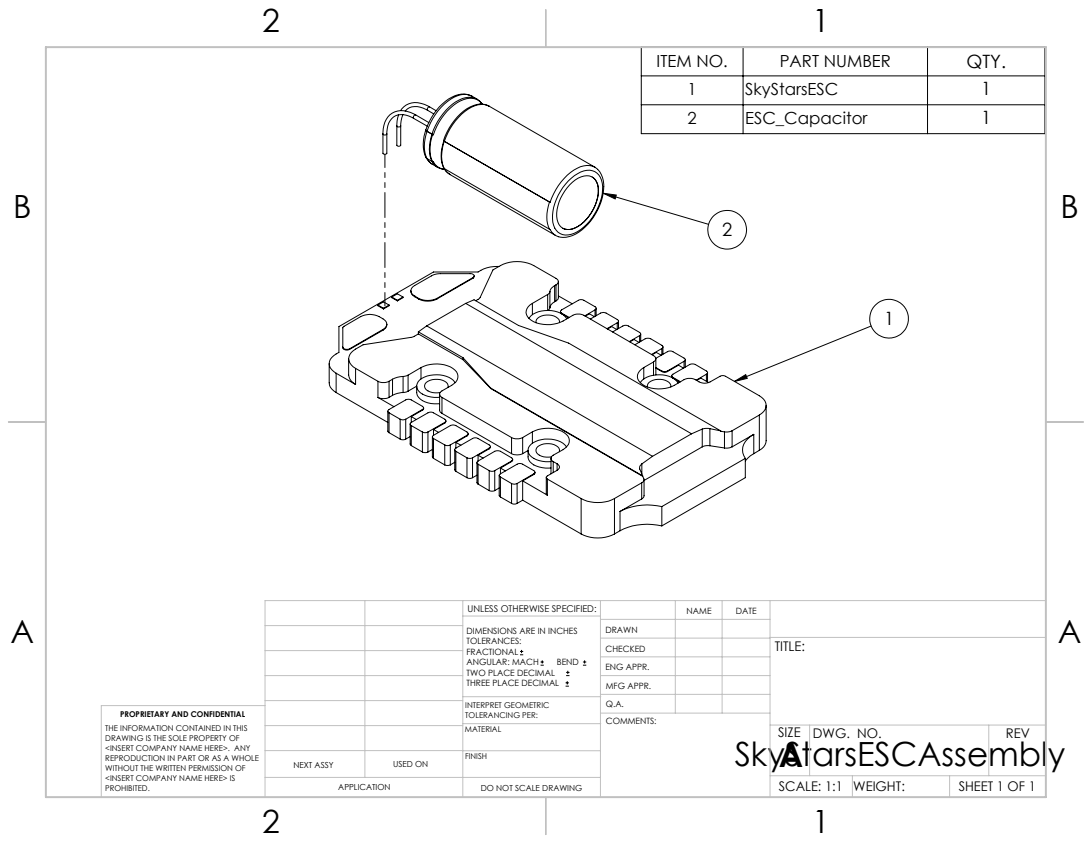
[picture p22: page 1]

ITEM NO. | PART NUMBER | QTY.
1 | SkyStarsESC | 1
2 | ESC_Capacitor | 1

UNLESS OTHERWISE SPECIFIED: | | NAME | DATE
DIMENSIONS ARE IN INCHES TOLERANCES: FRACTIONAL ANGULAR: MACH BEND TWO PLACE DECIMAL THREE PLACE DECIMAL | DRAWN

CHECKED | | | TITLE:

ENG APPR.
MFG APPR.

INTERPRET GEOMETRIC TOLERANCING PER: | Q.A.
MATERIAL | | SIZE A | DWG. NO. | REV

PROPRIETARY AND CONFIDENTIAL
THE INFORMATION CONTAINED IN THIS
DRAWING IS THE SOLE PROPERTY OF
<INSERT COMPANY NAME HERE>. ANY
REPRODUCTION IN PART OR AS A WHOLE
WITHOUT THE WRITTEN PERMISSION OF
<INSERT COMPANY NAME HERE> IS
PROHIBITED.

NEXT ASSY | USED ON | FINISH

APPLICATION | DO NOT SCALE DRAWING | | SCALE: 1:1 | WEIGHT: | SHEET 1 OF 1

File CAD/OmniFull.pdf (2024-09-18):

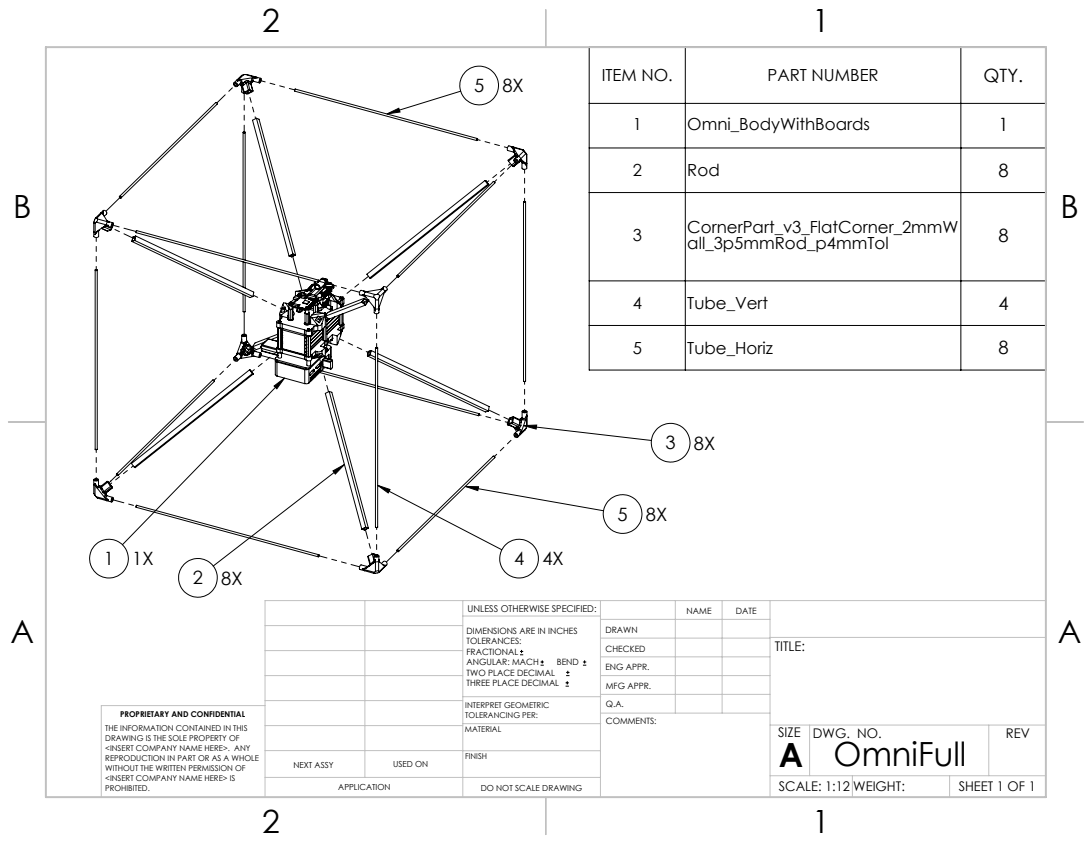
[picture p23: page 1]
ITEM NO.; PART NUMBER; QTY.

1 | Omni_BodyWithBoards | 1

2 | Rod | 8

3 | CornerPart_v3_FlatCorner_2mmW all_3p5mmRod_p4mmTol | 8

4 | Tube_Vert | 4

5 | Tube_Horiz | 8

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

CHECKED | | | TITLE:

ENG APPR.
MFG APPR.

INTERPRET GEOMETRIC TOLERANCING PER: | Q.A.
MATERIAL | | SIZE A | DWG. NO. OmniFull | REV

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

NEXT ASSY | USED ON | FINISH

APPLICATION | DO NOT SCALE DRAWING | | SCALE: 1:12 WEIGHT: | | SHEET 1 OF 1

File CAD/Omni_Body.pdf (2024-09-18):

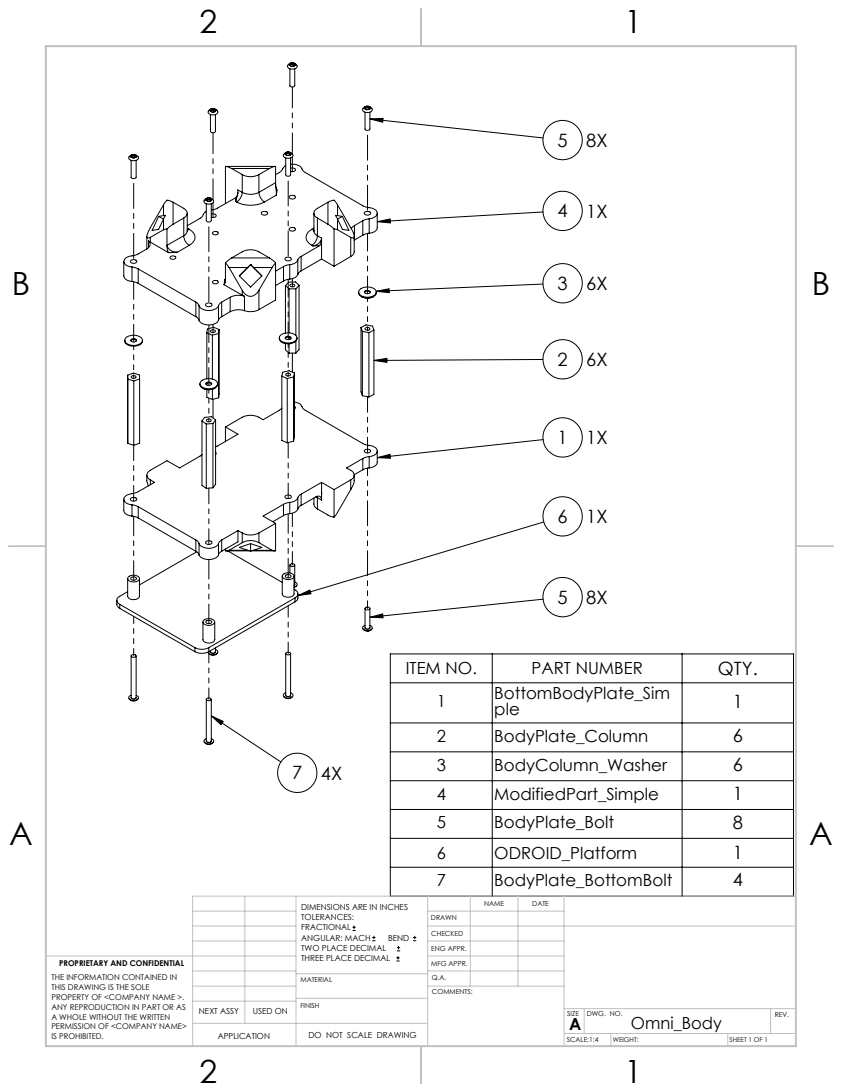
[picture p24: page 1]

ITEM NO. | PART NUMBER | QTY.
1 | BottomBodyPlate_Sim ple | 1
2 | BodyPlate_Column | 6
3 | BodyColumn_Washer | 6
4 | ModifiedPart_Simple | 1
5 | BodyPlate_Bolt | 8
6 | ODROID_Platform | 1
7 | BodyPlate_BottomBolt | 4

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

DRAWN
CHECKED
ENG APPR.

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

MATERIAL | Q.A.

NEXT ASSY | USED ON | FINISH

SIZE A | DWG. NO. Omni_Body | REV.

APPLICATION | | DO NOT SCALE DRAWING

SCALE:1:4 | WEIGHT: | SHEET 1 OF 1

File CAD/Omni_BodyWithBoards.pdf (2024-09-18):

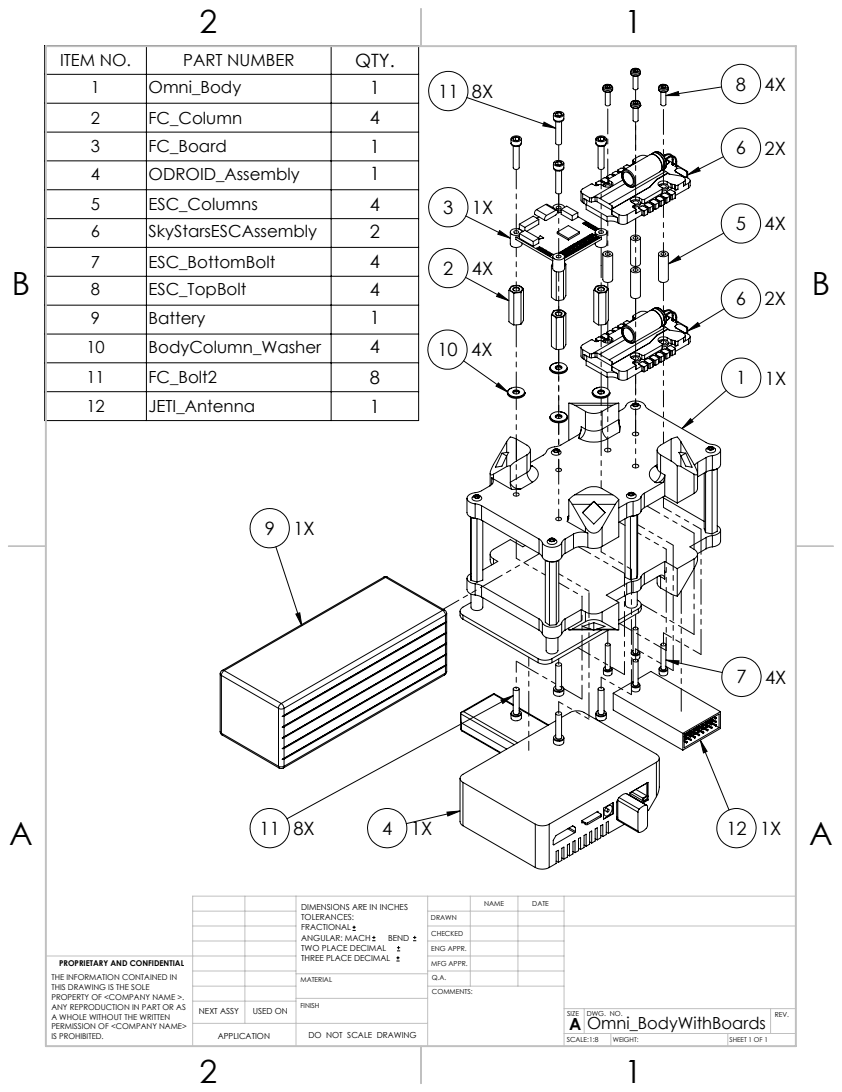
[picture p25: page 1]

ITEM NO. | PART NUMBER | QTY.
1 | Omni_Body | 1
2 | FC_Column | 4
3 | FC_Board | 1
4 | ODROID_Assembly | 1
5 | ESC_Columns | 4
6 | SkyStarsESCAssembly | 2
7 | ESC_BottomBolt | 4
8 | ESC_TopBolt | 4
9 | Battery | 1
10 | BodyColumn_Washer | 4
11 | FC_Bolt2 | 8
12 | JETI_Antenna | 1

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

DRAWN
CHECKED
ENG APPR.

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

MATERIAL | Q.A.

NEXT ASSY | USED ON | FINISH

SIZE A | DWG. NO. Omni_BodyWithBoards | REV.

APPLICATION | | DO NOT SCALE DRAWING

SCALE:1:8 | WEIGHT: | SHEET 1 OF 1

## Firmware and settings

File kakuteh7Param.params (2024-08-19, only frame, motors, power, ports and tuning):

1	1	BAT1_A_PER_V	14.775818824768066406	9
1	1	BAT1_CAPACITY	3300.000000000000000000	9
1	1	BAT1_I_CHANNEL	-1	6
1	1	BAT1_N_CELLS	6	6
1	1	BAT1_R_INTERNAL	0.004999999888241291	9
1	1	BAT1_SOURCE	-1	6
1	1	BAT1_V_CHANNEL	-1	6
1	1	BAT1_V_CHARGED	4.199999809265136719	9
1	1	BAT1_V_DIV	10.947239875793457031	9
1	1	BAT1_V_EMPTY	3.700000047683715820	9
1	1	BAT1_V_LOAD_DROP	0.100000001490116119	9
1	1	BAT_AVRG_CURRENT	15.000000000000000000	9
1	1	BAT_CRIT_THR	0.070000000298023224	9
1	1	BAT_EMERGEN_THR	0.050000000745058060	9
1	1	BAT_LOW_THR	0.150000005960464478	9
1	1	BAT_N_CELLS	6	6
1	1	BAT_V_CHARGED	4.199999809265136719	9
1	1	BAT_V_EMPTY	3.000000000000000000	9
1	1	BAT_V_LOAD_DROP	0.300000011920928955	9
1	1	BAT_V_OFFS_CURR	0.000000000000000000	9
1	1	CA_AIRFRAME	0	6
1	1	CA_ROTOR0_AX	0.209999993443489075	9
1	1	CA_ROTOR0_AY	-0.790000021457672119	9
1	1	CA_ROTOR0_AZ	0.579999983310699463	9
1	1	CA_ROTOR0_CT	6.500000000000000000	9
1	1	CA_ROTOR0_KM	-0.050000000745058060	9
1	1	CA_ROTOR0_PX	0.115823999047279358	9
1	1	CA_ROTOR0_PY	-0.115823999047279358	9
1	1	CA_ROTOR0_PZ	-0.115823999047279358	9
1	1	CA_ROTOR10_AX	0.000000000000000000	9
1	1	CA_ROTOR10_AY	0.000000000000000000	9
1	1	CA_ROTOR10_AZ	-1.000000000000000000	9
1	1	CA_ROTOR10_CT	6.500000000000000000	9
1	1	CA_ROTOR10_KM	0.050000000745058060	9
1	1	CA_ROTOR10_PX	0.000000000000000000	9
1	1	CA_ROTOR10_PY	0.000000000000000000	9
1	1	CA_ROTOR10_PZ	0.000000000000000000	9
1	1	CA_ROTOR11_AX	0.000000000000000000	9
1	1	CA_ROTOR11_AY	0.000000000000000000	9
1	1	CA_ROTOR11_AZ	-1.000000000000000000	9
1	1	CA_ROTOR11_CT	6.500000000000000000	9
1	1	CA_ROTOR11_KM	0.050000000745058060	9
1	1	CA_ROTOR11_PX	0.000000000000000000	9
1	1	CA_ROTOR11_PY	0.000000000000000000	9
1	1	CA_ROTOR11_PZ	0.000000000000000000	9
1	1	CA_ROTOR1_AX	-0.790000021457672119	9
1	1	CA_ROTOR1_AY	-0.209999993443489075	9
1	1	CA_ROTOR1_AZ	-0.579999983310699463	9
1	1	CA_ROTOR1_CT	6.500000000000000000	9
1	1	CA_ROTOR1_KM	-0.050000000745058060	9
1	1	CA_ROTOR1_PX	-0.115823999047279358	9
1	1	CA_ROTOR1_PY	-0.115823999047279358	9
1	1	CA_ROTOR1_PZ	-0.115823999047279358	9
1	1	CA_ROTOR2_AX	0.790000021457672119	9
1	1	CA_ROTOR2_AY	0.209999993443489075	9
1	1	CA_ROTOR2_AZ	-0.579999983310699463	9
1	1	CA_ROTOR2_CT	6.500000000000000000	9
1	1	CA_ROTOR2_KM	0.050000000745058060	9
1	1	CA_ROTOR2_PX	0.115823999047279358	9
1	1	CA_ROTOR2_PY	0.115823999047279358	9
1	1	CA_ROTOR2_PZ	-0.115823999047279358	9
1	1	CA_ROTOR3_AX	-0.209999993443489075	9
1	1	CA_ROTOR3_AY	0.790000021457672119	9
1	1	CA_ROTOR3_AZ	0.579999983310699463	9
1	1	CA_ROTOR3_CT	6.500000000000000000	9
1	1	CA_ROTOR3_KM	0.050000000745058060	9
1	1	CA_ROTOR3_PX	-0.115823999047279358	9
1	1	CA_ROTOR3_PY	0.115823999047279358	9
1	1	CA_ROTOR3_PZ	-0.115823999047279358	9
1	1	CA_ROTOR4_AX	0.209999993443489075	9
1	1	CA_ROTOR4_AY	-0.790000021457672119	9
1	1	CA_ROTOR4_AZ	-0.579999983310699463	9
1	1	CA_ROTOR4_CT	6.500000000000000000	9
1	1	CA_ROTOR4_KM	0.050000000745058060	9
1	1	CA_ROTOR4_PX	0.115823999047279358	9
1	1	CA_ROTOR4_PY	-0.115823999047279358	9
1	1	CA_ROTOR4_PZ	0.115823999047279358	9
1	1	CA_ROTOR5_AX	-0.790000021457672119	9
1	1	CA_ROTOR5_AY	-0.209999993443489075	9
1	1	CA_ROTOR5_AZ	0.579999983310699463	9
1	1	CA_ROTOR5_CT	6.500000000000000000	9
1	1	CA_ROTOR5_KM	0.050000000745058060	9
1	1	CA_ROTOR5_PX	-0.115823999047279358	9
1	1	CA_ROTOR5_PY	-0.115823999047279358	9
1	1	CA_ROTOR5_PZ	0.115823999047279358	9
1	1	CA_ROTOR6_AX	0.790000021457672119	9
1	1	CA_ROTOR6_AY	0.209999993443489075	9
1	1	CA_ROTOR6_AZ	0.579999983310699463	9
1	1	CA_ROTOR6_CT	6.500000000000000000	9
1	1	CA_ROTOR6_KM	-0.050000000745058060	9
1	1	CA_ROTOR6_PX	0.115823999047279358	9
1	1	CA_ROTOR6_PY	0.115823999047279358	9
1	1	CA_ROTOR6_PZ	0.115823999047279358	9
1	1	CA_ROTOR7_AX	-0.209999993443489075	9
1	1	CA_ROTOR7_AY	0.790000021457672119	9
1	1	CA_ROTOR7_AZ	-0.579999983310699463	9
1	1	CA_ROTOR7_CT	6.500000000000000000	9
1	1	CA_ROTOR7_KM	-0.050000000745058060	9
1	1	CA_ROTOR7_PX	-0.115823999047279358	9
1	1	CA_ROTOR7_PY	0.115823999047279358	9
1	1	CA_ROTOR7_PZ	0.115823999047279358	9
1	1	CA_ROTOR8_AX	0.000000000000000000	9
1	1	CA_ROTOR8_AY	0.000000000000000000	9
1	1	CA_ROTOR8_AZ	-1.000000000000000000	9
1	1	CA_ROTOR8_CT	6.500000000000000000	9
1	1	CA_ROTOR8_KM	0.050000000745058060	9
1	1	CA_ROTOR8_PX	0.000000000000000000	9
1	1	CA_ROTOR8_PY	0.000000000000000000	9
1	1	CA_ROTOR8_PZ	0.000000000000000000	9
1	1	CA_ROTOR9_AX	0.000000000000000000	9
1	1	CA_ROTOR9_AY	0.000000000000000000	9
1	1	CA_ROTOR9_AZ	-1.000000000000000000	9
1	1	CA_ROTOR9_CT	6.500000000000000000	9
1	1	CA_ROTOR9_KM	0.050000000745058060	9
1	1	CA_ROTOR9_PX	0.000000000000000000	9
1	1	CA_ROTOR9_PY	0.000000000000000000	9
1	1	CA_ROTOR9_PZ	0.000000000000000000	9
1	1	CA_ROTOR_COUNT	8	6
1	1	MC_PITCHRATE_D	0.003000000026077032	9
1	1	MC_PITCHRATE_FF	0.000000000000000000	9
1	1	MC_PITCHRATE_I	0.200000002980232239	9
1	1	MC_PITCHRATE_K	1.000000000000000000	9
1	1	MC_PITCHRATE_MAX	220.000000000000000000	9
1	1	MC_PITCHRATE_P	0.150000005960464478	9
1	1	MC_PITCH_P	6.500000000000000000	9
1	1	MC_ROLLRATE_D	0.003000000026077032	9
1	1	MC_ROLLRATE_FF	0.000000000000000000	9
1	1	MC_ROLLRATE_I	0.200000002980232239	9
1	1	MC_ROLLRATE_K	1.000000000000000000	9
1	1	MC_ROLLRATE_MAX	220.000000000000000000	9
1	1	MC_ROLLRATE_P	0.150000005960464478	9
1	1	MC_ROLL_P	6.500000000000000000	9
1	1	MC_YAWRATE_D	0.000000000000000000	9
1	1	MC_YAWRATE_FF	0.000000000000000000	9
1	1	MC_YAWRATE_I	0.100000001490116119	9
1	1	MC_YAWRATE_K	1.000000000000000000	9
1	1	MC_YAWRATE_MAX	200.000000000000000000	9
1	1	MC_YAWRATE_P	0.150000005960464478	9
1	1	MC_YAW_P	2.799999952316284180	9
1	1	MC_YAW_WEIGHT	0.400000005960464478	9
1	1	MOT_POLE_COUNT	14	6
1	1	MOT_SLEW_MAX	0.000000000000000000	9
1	1	PWM_MAIN_DIS1	900	6
1	1	PWM_MAIN_DIS2	900	6
1	1	PWM_MAIN_DIS3	900	6
1	1	PWM_MAIN_DIS4	900	6
1	1	PWM_MAIN_DIS5	900	6
1	1	PWM_MAIN_DIS6	900	6
1	1	PWM_MAIN_DIS7	900	6
1	1	PWM_MAIN_DIS8	900	6
1	1	PWM_MAIN_FAIL1	-1	6
1	1	PWM_MAIN_FAIL2	-1	6
1	1	PWM_MAIN_FAIL3	-1	6
1	1	PWM_MAIN_FAIL4	-1	6
1	1	PWM_MAIN_FAIL5	-1	6
1	1	PWM_MAIN_FAIL6	-1	6
1	1	PWM_MAIN_FAIL7	-1	6
1	1	PWM_MAIN_FAIL8	-1	6
1	1	PWM_MAIN_FUNC1	104	6
1	1	PWM_MAIN_FUNC2	103	6
1	1	PWM_MAIN_FUNC3	102	6
1	1	PWM_MAIN_FUNC4	101	6
1	1	PWM_MAIN_FUNC5	108	6
1	1	PWM_MAIN_FUNC6	107	6
1	1	PWM_MAIN_FUNC7	106	6
1	1	PWM_MAIN_FUNC8	105	6
1	1	PWM_MAIN_MAX1	1900	6
1	1	PWM_MAIN_MAX2	1900	6
1	1	PWM_MAIN_MAX3	1900	6
1	1	PWM_MAIN_MAX4	1900	6
1	1	PWM_MAIN_MAX5	1900	6
1	1	PWM_MAIN_MAX6	1900	6
1	1	PWM_MAIN_MAX7	1900	6
1	1	PWM_MAIN_MAX8	1900	6
1	1	PWM_MAIN_MIN1	1100	6
1	1	PWM_MAIN_MIN2	1100	6
1	1	PWM_MAIN_MIN3	1100	6
1	1	PWM_MAIN_MIN4	1100	6
1	1	PWM_MAIN_MIN5	1100	6
1	1	PWM_MAIN_MIN6	1100	6
1	1	PWM_MAIN_MIN7	1100	6
1	1	PWM_MAIN_MIN8	1100	6
1	1	PWM_MAIN_TIM0	-3	6
1	1	PWM_MAIN_TIM1	-3	6
1	1	PWM_MAIN_TIM2	-3	6
1	1	PWM_MAIN_TIM3	-3	6
1	1	SYS_AUTOSTART	8001	6

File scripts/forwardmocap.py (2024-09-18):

#!/usr/bin/env python3

import asyncio
import time
import mavsdk
from mavsdk import System
import numpy
import socket
import struct

from scipy.spatial.transform import Rotation

homeZ = 0
setHomeFlag = True


# Settings for ODROID connection
address_ODROID = "udp://:14560"

# Settings for Mocap connection
localIP     = "127.0.0.1"
localPort   = 12690
bufferSize  = 1024

NetMsgMat4_ID = 2807643820


# Create connection to Mocap network
async def createMocapUDPconnection():

    # Create a datagram socket
    UDPServerSocket = socket.socket(family=socket.AF_INET, type=socket.SOCK_DGRAM)

    # Bind to address and ip
    UDPServerSocket.bind((localIP, localPort))

    print("UDP server up and listening")

    return UDPServerSocket


# Create connection to PX4 through ODROID
async def createODROIDconnection():

    drone = System()
    await drone.connect(system_address=address_ODROID)

    #status_text_task = asyncio.ensure_future(print_status_text(drone))

    # Wait for drone connection
    print("Waiting for drone to connect...")
    async for state in drone.core.connection_state():
        if state.is_connected:
            print(f"-- Connected to drone!")
            break

    return drone


# Listen for incoming data from Mocap connection
def listenForIncomingData(UDPServerSocket, printtoggle):

    # Listen for message from socket
    bytesAddressPair = UDPServerSocket.recvfrom(bufferSize)

    # Extract message and address
    message = bytesAddressPair[0]
    address = bytesAddressPair[1]

    # clientMsg = "Message from Client:{}".format(message)
    # clientIP  = "Client IP Address:{}".format(address)
    # print(clientMsg)
    # print(clientIP)

    # Decode the message based on MsgName (int), payload (int), data
    netMsgID = int.from_bytes(message[0:4], 'big')
    payloadBytes = int.from_bytes(message[4:8], 'big')

    if (printtoggle):
        print("NetMsgID is ", netMsgID)

    return message, address, netMsgID, payloadBytes


# Parse NetMsgMat4 object
def parse_NetMsgMat4(message, printtoggle):

    if (printtoggle):
        print( "NetMsgMat4 arrived... Let's look inside" )

    mat4 = numpy.empty([4,4])
    unpack = struct.Struct(">d") #> means big endian
    i = 0
    for r, c in numpy.ndindex( mat4.shape ):
        f = unpack.unpack( bytes( message[8 + i*8 : 8+i*8 + 8] ) )
        # print( "f is", f[0] )
        mat4[c][r] = f[0]
        i = i + 1

    if (printtoggle):
        print(mat4)

    return mat4


# Convert Mat4 array to desired array of mocap values
#   Assumes mat4 format of:
#     [a00, a01, a02,   x;
#      a10, a11, a12,   y;
#      a20, a21, a22,   z;
#        0,   0,   0,   0];
def convertMat4toMocap(mat4):

    # Extract rotation matrix
    rotmat = Rotation.from_matrix(mat4[numpy.ix_([0, 1, 2], [0, 1, 2])])

    #print("Rotation matrix: ", rotmat)

    # Convert rotation matrix to Euler angles (rad)
    yaw, pitch, roll = rotmat.as_euler("ZYX", degrees=False)

    #print("Euler angles (rad): ", roll, ", ", pitch, ", ", yaw)

    global homeZ, setHomeFlag

    # if setHomeFlag:
    #     homeZ = mat4[2, 3]
    #     setHomeFlag = False

    # Return [x, y, z, roll, pitch, yaw]
    return numpy.array([mat4[0, 3], mat4[1, 3], mat4[2, 3] - homeZ, roll, pitch, yaw])


# Form MAVSDK Mocap Object from Mocap Data
def createMAVmocapObject(mocapData):

    # mocapData ENU to NED
    # TODO: CHANGE THIS TO FIT ACTUAL MOCAP FRAME
    n  =  mocapData[1]
    e  =  mocapData[0]
    d  = -mocapData[2]
    nr =  mocapData[4]
    ep =  mocapData[3]
    dy = -mocapData[5]  # + 3.14159

    # NED position vector
    posvec = numpy.array([n, e, d])

    # Attitude vector
    attvec = numpy.array([nr, ep, dy])

    # Default covariance matrix
    pose_covar = mavsdk.mocap.Covariance([float(0.1 ** 2), float(0), float(0), float(0), float(0), float(0),
                                          float(0.1 ** 2), float(0), float(0), float(0), float(0),
                                          float(0.1 ** 2), float(0), float(0), float(0),
                                          float(100), float(0), float(0),
                                          float(100), float(0),
                                          float(100)])

    # Position (m)
    position_body = mavsdk.mocap.PositionBody(float(posvec[0]), float(posvec[1]), float(posvec[2]))

    # Attitude (rad)
    angle_body = mavsdk.mocap.AngleBody(float(attvec[0]), float(attvec[1]), float(attvec[2]))

    # Return MAVSDK Mocap object
    return mavsdk.mocap.VisionPositionEstimate(0, position_body, angle_body, pose_covar)


# Send mocap data to ODROID
async def sendMocapData(drone, mocapData):

    # Create MAVSDK Mocap object from mocapData
    mocapObj = createMAVmocapObject(mocapData)

    # Send Mocap object to drone
    await drone.mocap.set_vision_position_estimate(mocapObj)


# Main script
async def main():

    # Print-to-screen frequency (Hz)
    printfreq = 10

    # Create a datagram socket
    UDPServerSocket = await createMocapUDPconnection()

    # Connect to ODROID
    drone = await createODROIDconnection()

    # Start time variables
    starttime_msg = time.time()
    starttime_print = starttime_msg

    # Continue to listen for incoming messages to forward to ODROID
    while True:

        endtime = time.time()

        # Listen for incoming messages
        message, address, netMsgID, payloadBytes = (
            listenForIncomingData(UDPServerSocket, False))

        # Message is NetMsgMat4
        if netMsgID == NetMsgMat4_ID:

            # Parse message into mat4 format
            mat4 = parse_NetMsgMat4(message, False)

            # Convert mat4 into mocap data array
            mocapData = convertMat4toMocap(mat4)


            # Send mocap data to ODROID
            try:
                await sendMocapData(drone, mocapData)
            except:
                print("ERROR SENDING MOCAP")
                continue


            # Print mocapData to console at set frequency
            if (endtime - starttime_print) > (1/printfreq):
                starttime_print = time.time()
                print(mocapData)


# (UNUSED) Print status updates from ODROID
async def print_status_text(drone):
    try:
        async for status_text in drone.telemetry.status_text():
            print(f"Status: {status_text.type}: {status_text.text}")
    except asyncio.CancelledError:
        return


# Run main script
if __name__ == "__main__":
    # Run the asyncio loop
    asyncio.run(main())

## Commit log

2024-09-18 Fixed errors with mavserver and StartUpD documentation
    [mavserver.py]
2024-09-18 Added CAD files detailing the omnicopter assembly
    [3DPrintedCornerOutside.stl, Battery.SLDPRT, BodyColumn_Washer.SLDPRT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]
